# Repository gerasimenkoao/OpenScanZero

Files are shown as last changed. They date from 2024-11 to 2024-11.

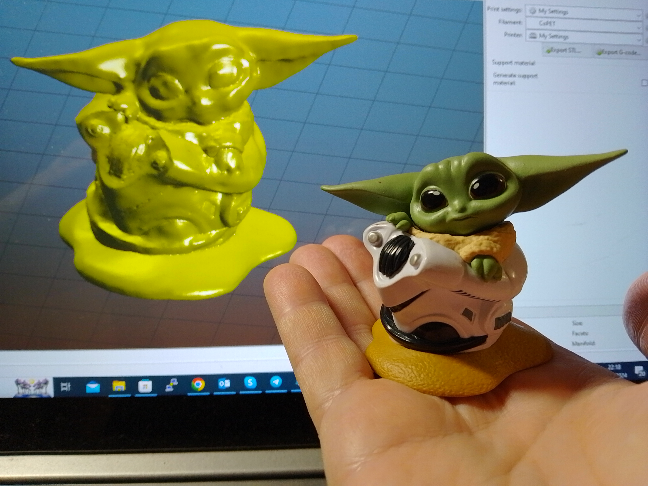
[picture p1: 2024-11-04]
0.jpg

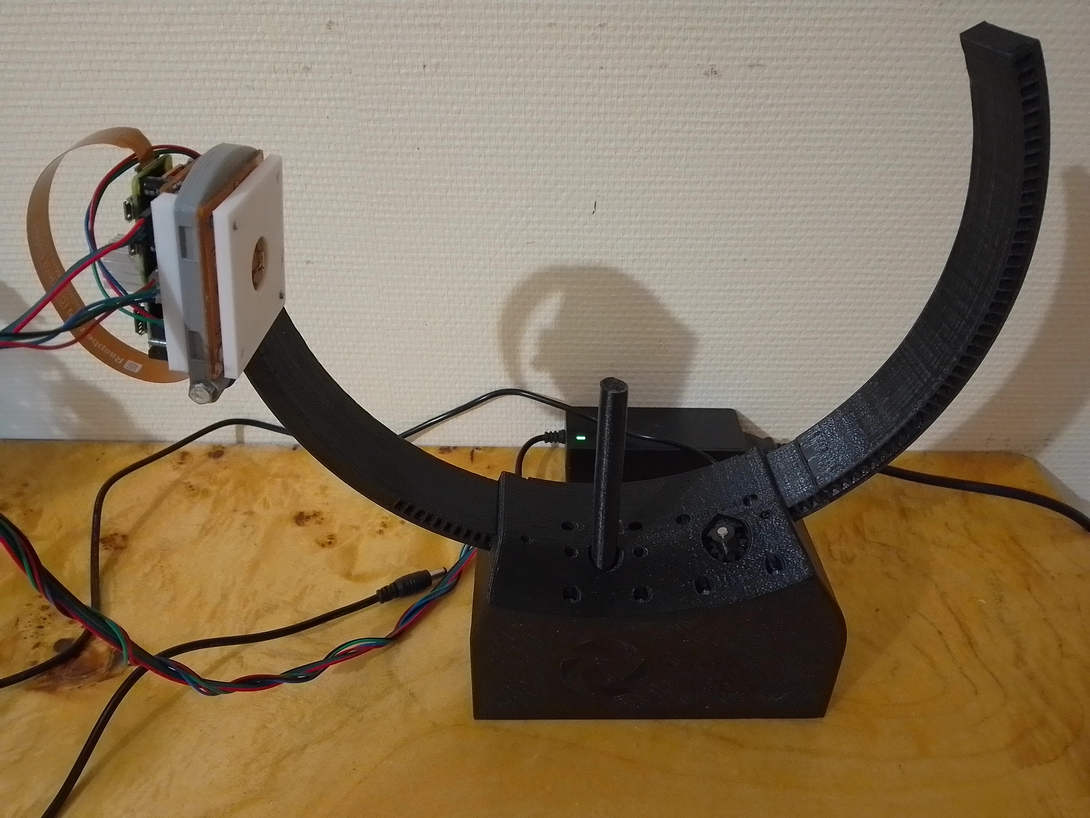
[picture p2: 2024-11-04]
6.jpg

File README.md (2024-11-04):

# OpenScanZero
The cheapest OpenScan Zero 3D scanner project (Mini/Midi)

The title is true if you have a mini milling machine and a Raspberry Zero 2W ;-)
Raspberry zero differs in minimal configuration, so I got rid of the optional connector in my scanner.
The advantages of the project are a lower price and no problems with the camera.

Equipment:

3D-Printer, for example Anet A8 or Prusa I3 (any FDM with 200x200mm print area)
Mini milling machine (i use CNC 1610)
Soldering iron and solder
Tester

Materials:

coPET/PET-g filamet (depends to project type up to 500 grams)
one-sided foiled fiberglass for PCB - two plates 90x70mm or one with similar area.
Raspbery Zero 2W with 16+ Gb microSD card 
IMX519 or Raspberre camera V3 with cable for RasPi Zero. 
two a4988 drivers
two 100uF 16v & two 100nF capacitors
two IRLZ34/IRLZ44 mosfet (you need to cut-off heatsink on it)
two curved pin Header male, 4p, 2.54
LM7805 or better step-down 5V 1A replacement
Pin Header female, 2x20p, 2.54
Barrel Connector, 5.5-2.1mm

two NEMA-17 stepper motor with 50-sm. wires

Eight 1W-led
two resistors 1 ohm
three 26AWG 20sm.-lenght wire 

Varnish for PCB (I have clear)

12V 2A Power Supply

Resources:

You need to download & print scanner parts from https://github.com/OpenScan-org/OpenScan-Design
!!!!!One more thing is needed - a Zero shield holder - just from here - file Mount.stl

Download OpenScan Composer software and firmware from https://www.openscancomposer.com/
Flashing and install manual you can find on that site too.

Development:

Download pcb models 4 OpenScan Zero shield & RingLight just from here - files OpenScanZero.GBR & RingLight.GBR
Mill it ( present modells in Gerber mirrored format) - i use FlatCam for processing and Candle for milling

3. Drill the mounting holes in the RingLight board with a 4mm drill and the central hole for the camera 16mm
4. Solder LEDs and resistors on it. Observe the polarity - there are two groups of LEDs in series.
5. Check the functionality of the LEDs by connecting red to +12V and green, blue to minus. Cover the board with varnish.

6. Solder the power connector and jumpers to the shield board
7. Solder capacitors, connectors and transistors. They should not touch the jumpers
8. Solder the stepper motor drivers & Pin Header female.
9. Connect the power supply. Did the smoke not go away? Perfectly! Adjust the current of the a4988 drivers.
10. Solder the connectors on the Raspberry pi with the pins facing down. Insert the microSD firmware into the Raspberry and its into the shield.
11.  Still no smoke and the LEDs flashed a few times? Great! Print plastic parts!
12. The compilation process is described at https://openscan-org.github.io/OpenScan-Doc/

The camera is fixed with double-sided tape. OpenScan shield is attached with glue.

Yes, the system is far from ideal, but it worked for me the first time

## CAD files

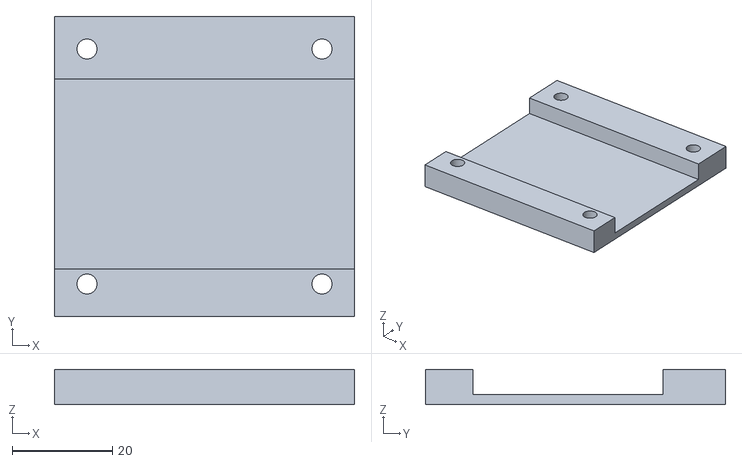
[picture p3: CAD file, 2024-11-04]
Mount.stl
60.0 x 60.0 x 7.00
